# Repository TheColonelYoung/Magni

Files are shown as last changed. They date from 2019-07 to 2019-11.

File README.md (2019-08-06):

# Magni
Electric linear actuator powered by stepper motor. Based on 3D printed body with built-in bearing.

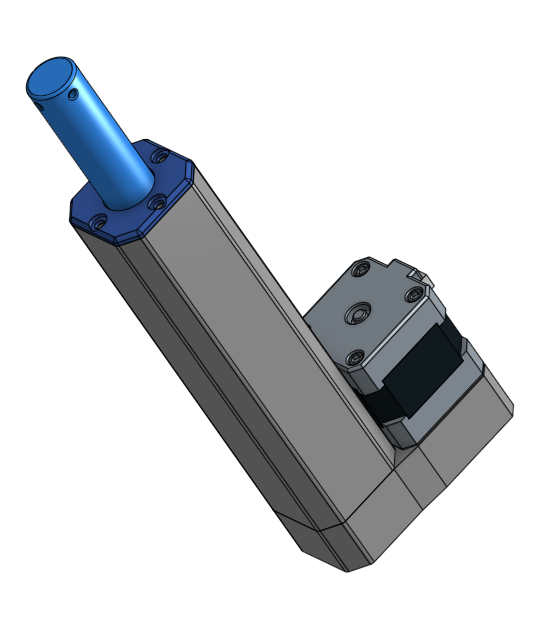
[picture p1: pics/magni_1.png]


Actuator is easily modifiable, with with any length. There are only two parts which needs to be modified for greater length.
Project is designed in Onshape. Project can be downloaded or forked on this [link](https://cad.onshape.com/documents/d29122f55449fc9b32e37efc/w/e29782a3cd26bfe716aed0ac/e/d3b8e881492a84b656a9ecee)

Actual version have mounting holes for NEMA17 motor. Motion from motor is transmitted from motor to trapezoid rod via GT2 belt.
Belts are mounted on 32 teeth gears. Gears are printed from HIPS, so are more stiffer.
Ration between motor rotation and actuator shift is 3 mm shift per 1 rotation if motor.
Maximal achievable speed is around 20mm/s with common motor.

Inside shaft is fixed printed T-nut. Commercial steel nut not fit into this tight space. This nut is best to print from HIPS because is one of the most the stiffest material from from commercially available (another possibility is carbon fibber filled PLA). Nut is fixed in shaft by 4 worm screws.

Possible issue is with stability of push rod.
This can be resolved by mounting trapezoid into bearings.
But bearings need to be perfectly in line, because otherwise can be bearing damaged by turning of main rod.
Stability can be upgraded with better stability of body, this can be achieved by more mounting screws between gearbox and body.

### Build-in bearings
This gcode can be placed into marked layer to stop during print. During pause can be bearing inserted, after it print can be resumed by pressing a button.
Issue can be if you are using sticky parameter. So speed of command after this block can be affected by last used speed.
```gcode
G91
G1 E-6 F4800
G1 Z50 F600
M300 S300 P1000
M0 Click to continue...
G1 Z-50 F600
G1 E6.5 F4800
G90
```

# Pictures
### **Open gearbox**
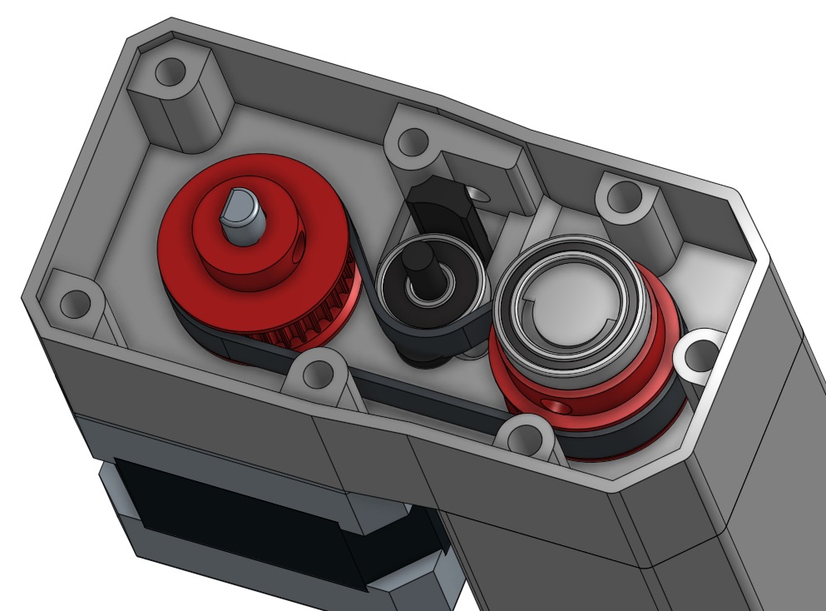
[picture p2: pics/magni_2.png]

### **Cross section of shaft**
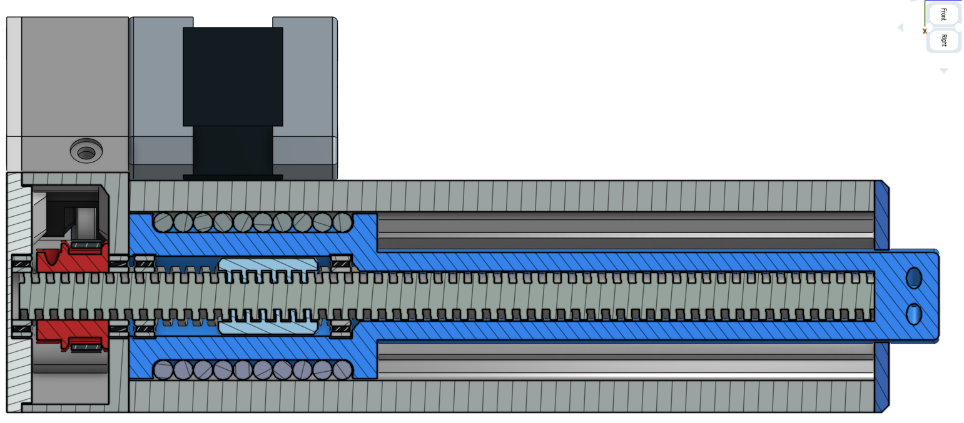
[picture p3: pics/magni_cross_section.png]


## Main parts
- [Shaft](STL/Shaft.stl)
- [Body](STL/Body.stl)
- [Front cover](STL/Front_cover.stl)
- [Back cover](STL/Cover_back.stl)
- [Pulley - motor](STL/Pulley_32T_B5.stl)
- [Pulley - trapezoid](STL/Pulley_32T_B12.stl)
- [Gearbox - base part](STL/Gearbox_body.stl)
- [Tensioner head](STL/Tensioner_head.stl)
- [Trapezoidal nut](STL/T-nut.stl)

## Other parts
- Bearings
    - 4x12x4, 1 pcs
    - 12x18x4, 4pcs
- Belt - GT2, 155mm closed loop belt
- Trapezoidal screw rod T12 - length 172mm
- Steel bearing balls - diameter 4mm, 40 pcs
- Screws - TODO

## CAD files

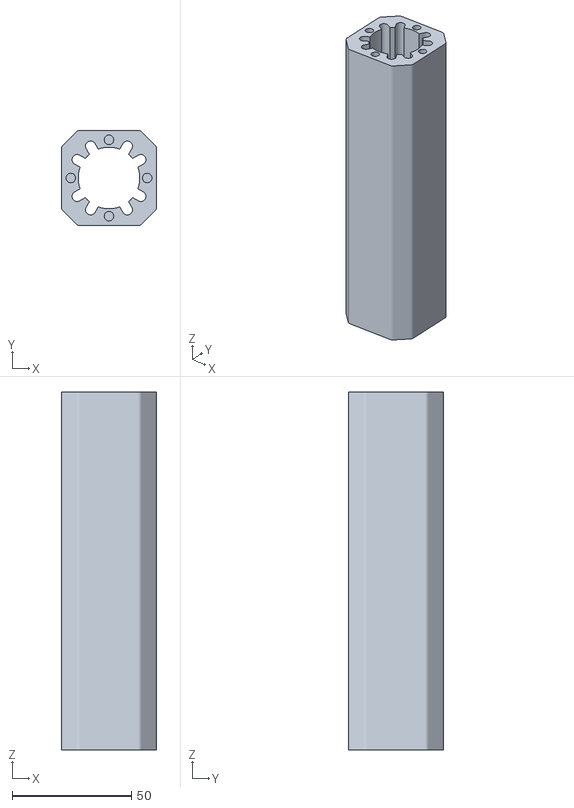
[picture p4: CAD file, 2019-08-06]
STL/Body.stl
40.0 x 40.0 x 150.0

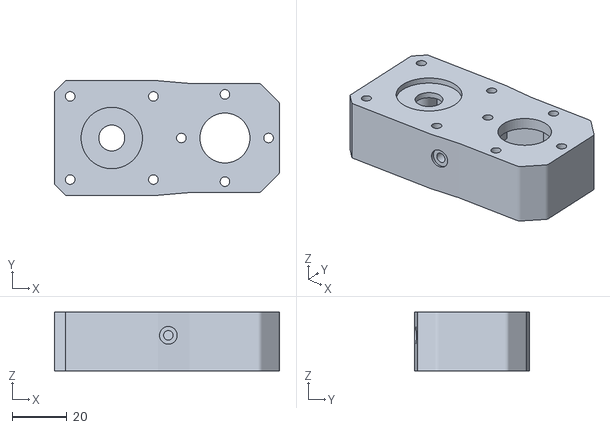
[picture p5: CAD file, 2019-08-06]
STL/Gearbox_body.stl
82.5 x 42.0 x 21.5

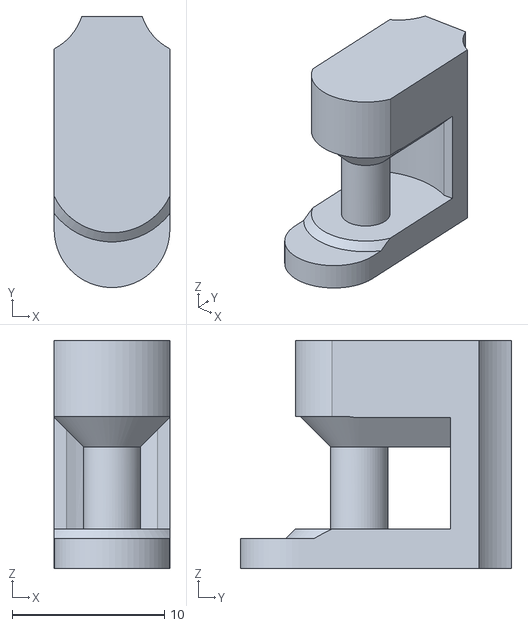
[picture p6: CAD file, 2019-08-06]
STL/Tensioner_head.stl
7.60 x 17.8 x 15.0

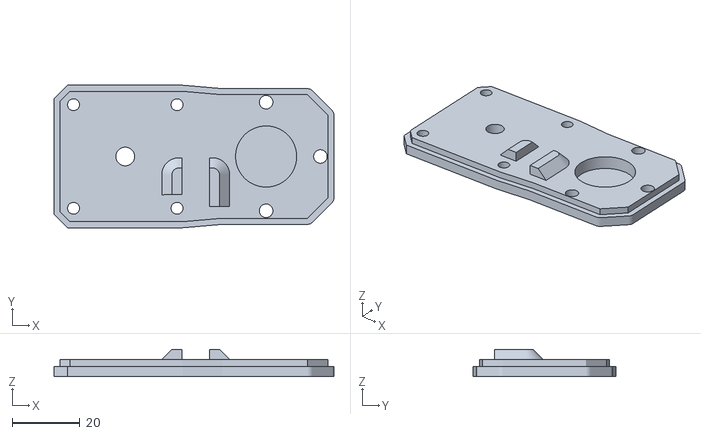
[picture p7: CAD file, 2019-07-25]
STL/Gearbox_cover.stl
82.5 x 42.0 x 8.00

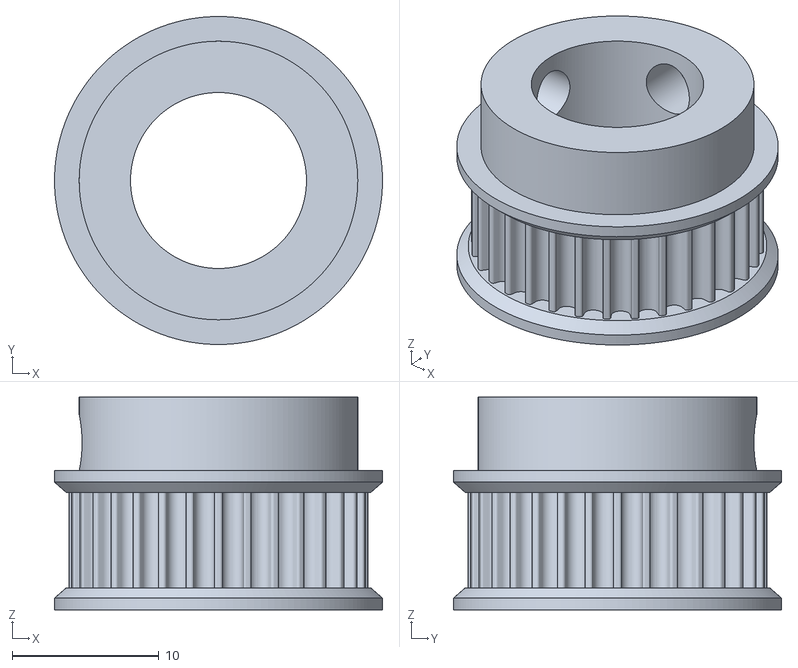
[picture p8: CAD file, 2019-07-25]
STL/Pulley_32T_B12.stl
22.4 x 22.4 x 14.5

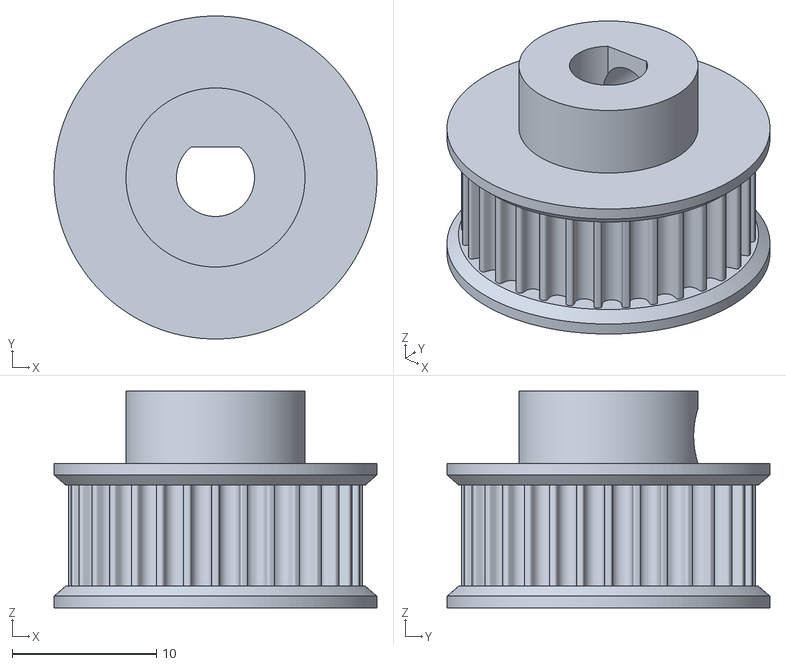
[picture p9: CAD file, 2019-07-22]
STL/Pulley_32T_B5.stl
22.4 x 22.4 x 15.0

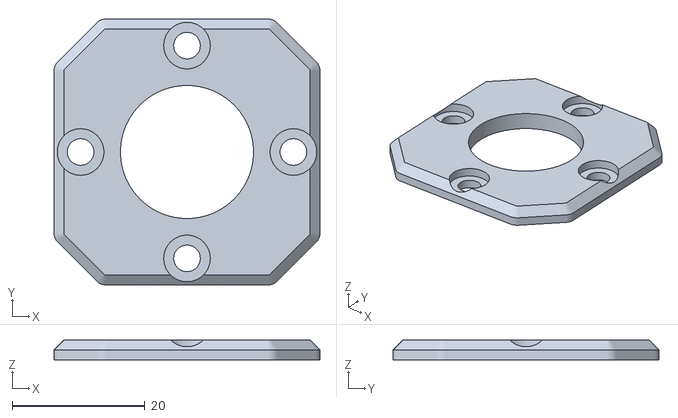
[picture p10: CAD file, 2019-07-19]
STL/Front_cover.stl
40.0 x 40.0 x 3.00

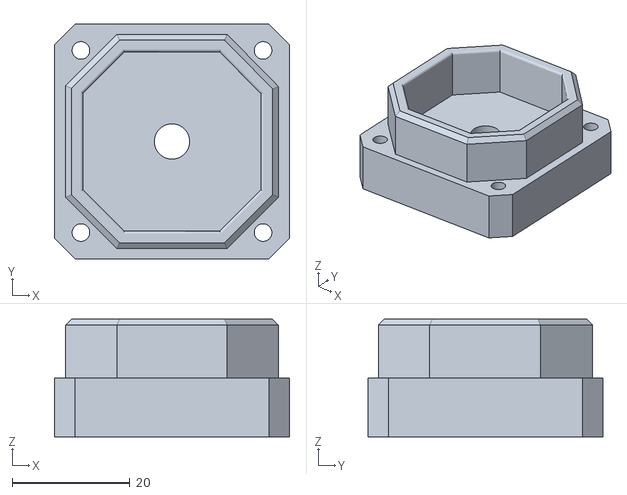
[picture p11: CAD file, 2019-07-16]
STL/Cover_back.stl
40.0 x 40.0 x 20.0

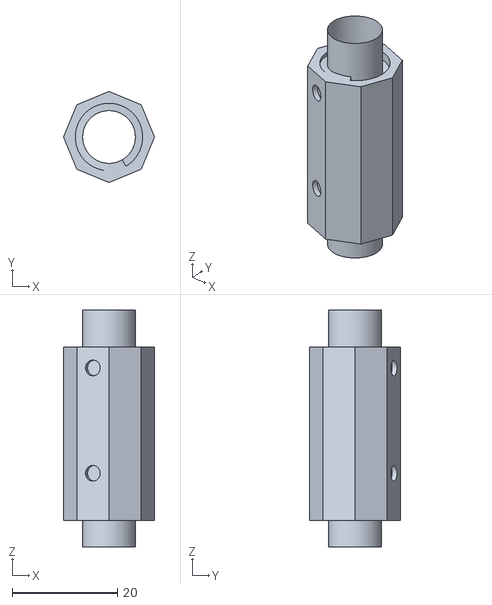
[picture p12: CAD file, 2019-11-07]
STL/T-nut.stl
17.3 x 17.3 x 45.0

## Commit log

2019-07-16 STL: add STl for basic parts, update of README
    [Body.stl, Cover_back.stl]
2019-07-19 STL - Body: Change of basic size of body to 40mm
    [Body.stl, Front_cover.stl]
2019-07-21 STL: add GT2 pulley with 30 teeth for motor shaft
    [Pulley_30T_B5.stl]
2019-07-21 STL: Fixed motor pulley bore size
    [Pulley_30T_B5.stl]
2019-07-21 STL: Add pulley for bore trapezoidal rod with 30 teeth
    [Pulley_30T_B12.stl]
2019-07-21 STL: add basic sketch of gearbox body
    [Gearbox_body.stl]
2019-07-21 Notes: update of STL list, add notes about gear rations and speed
2019-07-22 Pulley: modified pulley to version with 32 teeth
    [Pulley_30T_B12.stl, Pulley_30T_B5.stl, Pulley_32T_B12.stl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]
2019-07-22 Gearbox: update gearbox for 32 teeth pulley
    [Gearbox_body.stl]
2019-07-23 Notes: add part about stability of push rod
2019-07-24 STL: add gearbox with space for tensioner, add tensioner head for 13mm bearing
    [Gearbox_body.stl, Tensioner_head.stl]
2019-07-24 STL: add cover for gearbox, with lining for tensioner
    [Gearbox_cover.stl]
2019-07-25 STL: new revision of pulleys, updated tensioner head
    Pulley how have only 6.5 iwdth space for belt (moved from 7mm).
    Tensioner is now higher, so can placed into rails of gearbox cover.
    [Pulley_32T_B12.stl, Tensioner_head.stl]
2019-07-25 STL: new version of gearbox with cover
    Cover now have mounting holes with inset holes for screw heads.
    Gearbox body is now higher and contains space for 18x12x4 bearing.
    This bearing is for trapezoid, due to better stability of push rod.
    [Gearbox_body.stl, Gearbox_cover.stl]
2019-07-28 Shaft: updated internal structure of shaft with build-in bearings
2019-08-02 Shaft: add second built-in bearing to lower part for better stability
2019-08-02 Notes: removed unnecessary picture of gearbox from top of README
2019-08-03 T-nut: add nut for trapezoid screw rod
    [Trapezoidal_nut.stl]
2019-08-03 T-nut: bigger middle hole of nut for better slight around rod
    [Trapezoidal_nut.stl]
2019-08-03 Notes: add T-nut into stl file list
    [T-nut.stl]
2019-08-03 Notes: add section with description of T-nut
2019-08-06 STL: new version of tensioner head with print-in bearing
    [Tensioner_head.stl]
2019-08-06 Notes: add example of gcode for pause in middle of print
2019-08-06 Tensioner: increase of bearing height, tested with print pause
    [Tensioner_head.stl]
2019-08-06 T-nut: removed surfaced inside T-nut
    [T-nut.stl]
2019-08-06 Shaft: smaller holes for 18mm bearings
2019-08-06 Gearbox: smaller holes for 18mm bearings (18.5 -> 18.3)
    [Body.stl, Gearbox_body.stl]
2019-08-06 T-nut: bigger middle hole for trapezoidal rod
    [T-nut.stl]
2019-11-07 T-nut: new version of longer T-nut with tighter and tested offsets
    [T-nut.stl]
2019-11-07 Shaft: update of internal space and mounting for inner T-nut
